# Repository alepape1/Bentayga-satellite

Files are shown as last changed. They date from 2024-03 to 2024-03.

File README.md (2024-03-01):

# Bentayga Cubesat

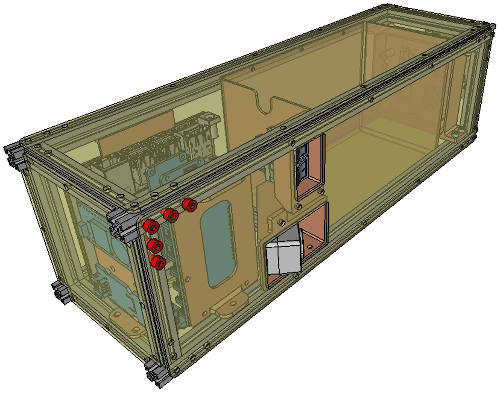
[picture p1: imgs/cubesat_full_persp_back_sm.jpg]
Bentayga Cubesat


## Description

This project describes the Bentayga 3U cubesat, developed by [IUMA](https://www.iuma.ulpgc.es/) at the [University of Las Palmas de Gran Canaria](https://www.ulpgc.es/).

The project is composed by three main parts:

- Structure made of 10x10 profiles, 3D printed parts and CNC milled FR4 fiberglass
- [Multispectral image acquisition](#multispectral-image-acquisition), composed by a Jetson Nano, 4 cameras with filters
- [Control and Flight manager](#flight-manager), composed by an Arduino MKR WAN 1310, with sensors such as GPS, temperature, humidity, barometer, RTC, IMU, and also controls the temperature of the batteries by activating heat pads.

---

## Bill Of Materials

[BOM](./bom_bentayga_cubesat.ods)

---

## [Assembly instructions](./assembly)

Assembly instructions are in [assembly directory](./assembly)

---

## [Structure](./cad)

Bentayga Cubesat

CAD files are in [Structure](./cad) directory.

## [Multispectral image acquisition](./CameraBoard)

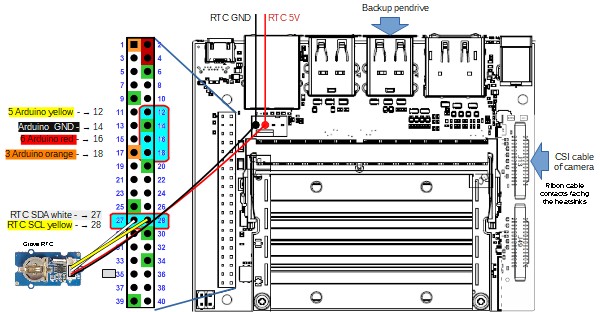
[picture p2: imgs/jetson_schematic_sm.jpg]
Jetson Nano connections


[Larger image of Jetson Nano connections](./imgs/jetson_schematic.jpg)

More information and source code is in [Camera board](./CameraBoard)

---

## [Flight manager](./Firmware)

The Flight Manager is responsible for gathering flight data from the IMU, sensors and transmitting it via LoRa to a ground station. It is also responsible of keeping batteries warm.

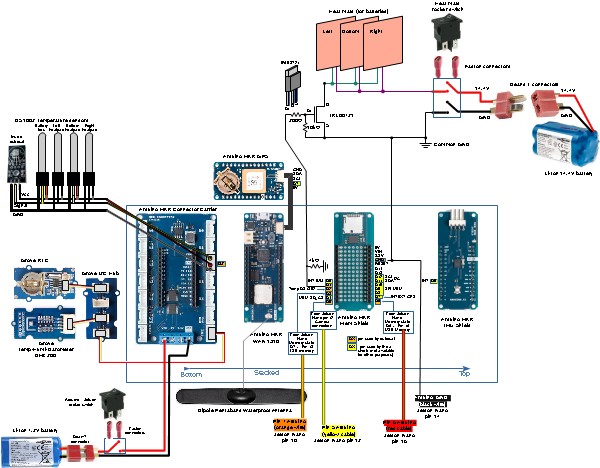
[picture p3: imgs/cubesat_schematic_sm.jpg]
Flight manager


[Larger image of electronics schematic](./imgs/cubesat_schematic.jpg)

More information and source code is in [Firmware](./Firmware)

---

## Contributing

If you wish to contribute to this code, please create a new branch from the develop branch and submit a pull request. 

---

## License

This code is licensed under the MIT License.

---

## CAD Images

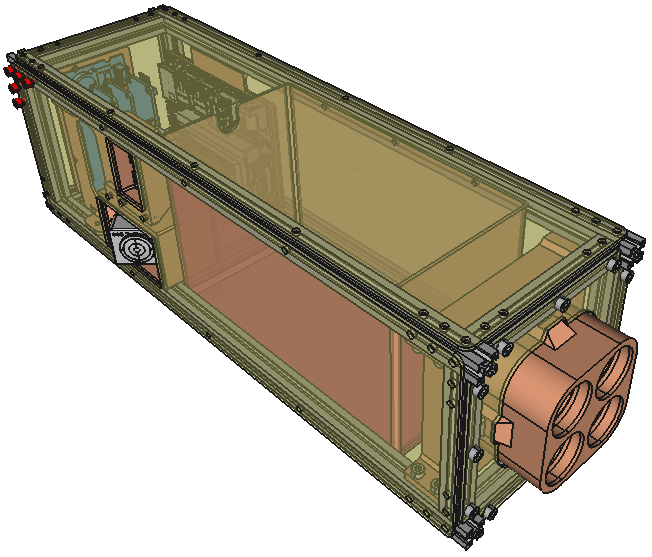
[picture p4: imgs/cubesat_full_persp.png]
Bentayga Cubesat front


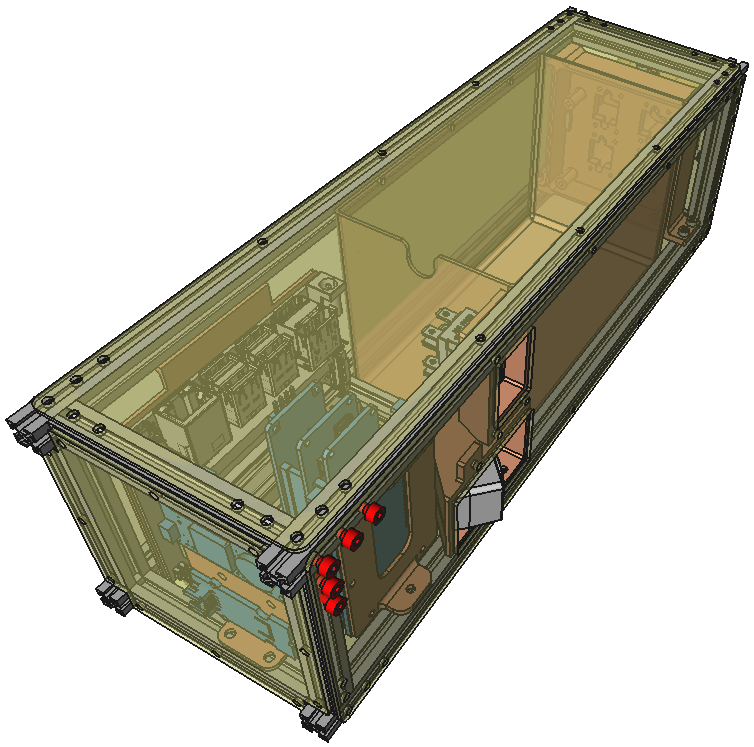
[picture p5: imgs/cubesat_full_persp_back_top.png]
Bentayga Cubesat back front


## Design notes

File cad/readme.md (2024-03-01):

# CAD files

There are 6 plates that have to be cutted or printed.

The references are as follows
Cielo and Tierra are the small sides, looking to the Sky and Earth.

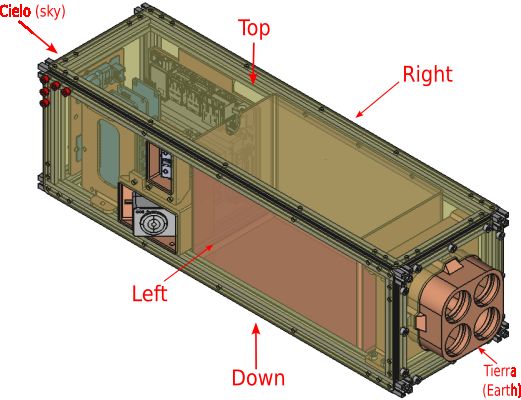
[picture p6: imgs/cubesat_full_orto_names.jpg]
References


Top and right plates are the placa_simple.
The others have the names in the file name.

## [DXF files](./dxf)

2D files for the plates, to cut them.

## [IGES files](./iges/placas)

3D files for the plates, to cut them.

## [FreeCAD files](./fcad)

Original FreeCAD files

## [PDF files](./pdf)

Files are for the plates, to laser cut.
Top and right plates use placa_simple.pdf

## [SVG files](./svg)

Also for the plates, you can edit them using Inkscape.

## [STEP files](./step)

These files are for the 3D parts, in a parametric format that most tools can read

## [STL files](./stl)

These files are for the 3D parts to print. You can print them without a support.

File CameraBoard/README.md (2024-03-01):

# Camera Capturing Platform

In this document the hardware and the software of the camera that is used to capture with the camera is described. 

## Hardware

### Jetson Nano Connections

The following scheme shows where to connect the external cables to the board that controls the camera capturing process. For the GPIO connections, refer to the [following list](#gpio-connection-list).

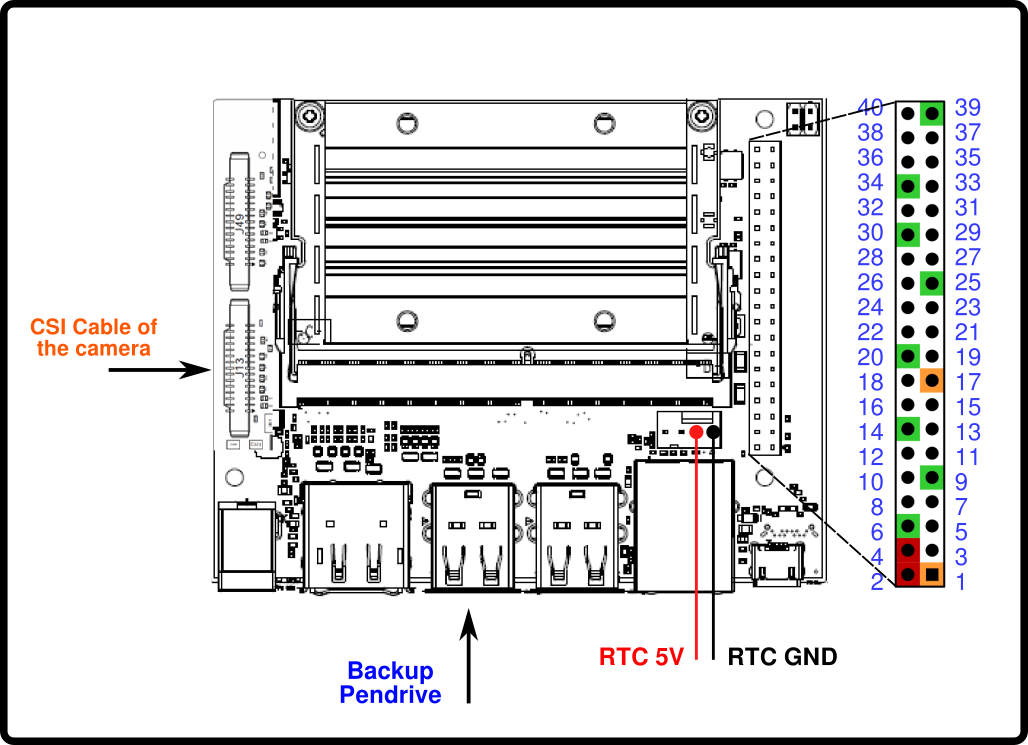
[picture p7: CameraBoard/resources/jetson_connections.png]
Jetson Nano Connection Scheme


#### GPIO connection list

* **Pins 1 - 6**: connect them to the six pin header of the camera.
* **Pin 12**: *Camera connection pin*. Connect it to the GPIO 5 in the Arduino.
* **Pin 16**: *Memory State LSB*. Connect it to the GPIO 6 in the Arduino.
* **Pin 18**: *Memory State MSB*. Connect it to the GPIO 7 in the Arduino.
* **Pin 27**: Connect it to the **SDA** pin of the **RTC**.
* **Pin 28**: Connect it to the **SCL** pin of the **RTC**.

## Software

### Installation

#### Initialize the process when the board is plugged in.

To execute the capturing code when the board is turn on, a custom service must be created. The service used is stored in the **.service** folder by the name of *camera-process.service* . The first step is to modify the document with the name of the current user and the current path of the *.sevice/execute_script.sh* file. Once the service points to the correct path, give execution permission to the *execute_script.sh* file. After that, execute the following commands to enable the service:

```bash
sudo cp .services/camera-process.service /etc/systemd/system
sudo systemctl start camera-process.service
sudo systemctl enable camera-process.service
```

The script will be executed once the board boots again. To stop the process after the start, run:

```bash
sudo systemctl stop camera-process.service
```

To check the status of the script, run the following command:

```bash
sudo systemctl status camera-process.service
```

To prevent the script to execute at the startup, run:

```bash
sudo systemctl disable camera-process.service
```

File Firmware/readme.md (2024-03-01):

# Flight manager:

Flight manager

[Larger image of electronics schematic](../imgs/cubesat_schematic.jpg)

The main stack of arduino boards is the following from bottom to top:

- MKR connector: https://docs.arduino.cc/hardware/mkr-connector-carrier
- MKR WAN 1310: https://docs.arduino.cc/hardware/mkr-wan-1310
- MKR MEM SHIELD: https://docs.arduino.cc/hardware/mkr-mem-shield
- MKR IMU SHIELD: https://docs.arduino.cc/hardware/mkr-imu-shield

Then there are other boards connected by I2C

- MKR GPS Shield: connect to the ESLOV connector https://docs.arduino.cc/hardware/mkr-gps-shield
- Grove - Temp&Humi&Barometer Sensor (BME280) https://www.seeedstudio.com/Grove-BME280-Environmental-Sensor-Temperature-Humidity-Barometer.html
- Grove - DS1307 RTC (Real Time Clock) for Arduino https://www.seeedstudio.com/Grove-RTC-DS1307.html

The temperature sensors are connected directly by Onewire protocol:

- DS18B2 temperature sensors [see below](#Temperature-sensors)

Finally, the heatpads are connected through a board that includes the MOSFET to control them (we have soldered the board) [see below](#Temperature-control)

### Requirements

This code requires the following libraries:
- Wire.h
- MS5x.h
- MKRIMU.h
- LoRa.h

Using the Arduino Library manager, search and install the following packages:

* BNO055 - Adafruit; and it dependencies.
* BM280 - Adafruit; and it dependencies.
* Groove RTC DS1307 - Speeed Studio
* OneWire https://playground.arduino.cc/Learning/OneWire
* Dallas Temperature: https://www.milesburton.com/w/index.php/Dallas_Temperature_Control_Library

### Setup

The Flight Manager should be connected to an IMU and a barometric pressure sensor. The LoRa module should also be properly connected.

### Usage

Upon startup, the Flight Manager will attempt to connect to the barometric pressure sensor. Once connected, it will continuously poll the sensor for data and transmit it via LoRa. Flight data is formatted into a byte array that includes start and stop bytes, as well as the following data:
- Roll
- Pitch
- Heading
- Temperature
- Pressure
- Sea level pressure
- Altitude
- Corrected altitude

In addition to transmitting the data, the Flight Manager also prints it to the serial monitor.

-------------------

## [Temperature sensors](./temperature)

Arduino code to identify and request temperature from the OneWire
 [DS18B20](https://www.analog.com/media/en/technical-documentation/data-sheets/ds18b20.pdf) temperature sensor, and to control the heatmats

Use libraries:

- https://playground.arduino.cc/Learning/OneWire
- https://www.milesburton.com/w/index.php/Dallas_Temperature_Control_Library

The cubesat has five DS18B20 temperature sensors, whose internal codes referred to the cubesat laid down and from the camera side, are:

Sensors inside the battery box
- Right (Derecha):  28 53 6E 95 F0 01 3C EE (waterproof sensor)
- Left (Izquierda): 28 37 50 95 F0 01 3C D7 (waterproof sensor)
- Down (Bajo):      28 7A EF 95 F0 01 3C C8 (waterproof sensor)
- Inside box:       28 55 B3 95 F0 01 3C EE (waterproof sensor)
- Inside cubesat:   28,FF 10 4B 20 18 01 10 (PCB sensor with resistor)

---

## Reference

Since there are 5 temperature sensors, 3 of them at the sides of the batteries. To know which sensor is each of them, the reference is taken from the following picture, considering I the left (Izquierda), and R the right (Derecha)

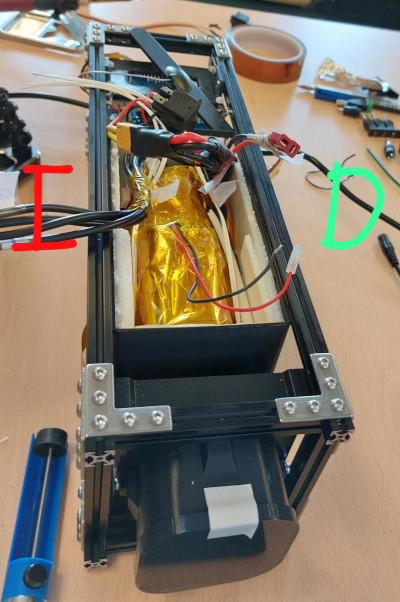
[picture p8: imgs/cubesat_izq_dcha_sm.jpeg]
Bentayga Cubesat Reference


### [Detect sensor ID](./temperature/detect_ds1820_tempsens_id/)

Get the sensor ID, better to have just one sensor to know the ID, because it will print all the sensors ID found.

As explained in the datasheet, there are two options for the sensor connection, we have used the one with external supply, using as VDD the 5V of the Arduino. 
A 4.7 Ohm resistor is needed, but the board sensor already has one. In the other cases, you will need to connect it.

Various sensor can be connected in multidrop, with multiple slaves.

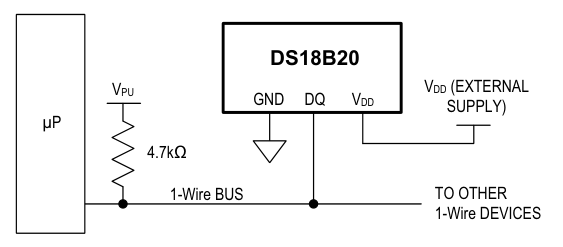
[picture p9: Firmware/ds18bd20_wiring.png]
DS18D20 wiring


### [Get sensor temperature](./temperature/get_temp_ds18b20_wid/)

Having the IDs of the sensor, it will request their temperatures.

Since one of the sensors is in a board with a resistor, an additional resistor is not needed.

### [Temperature control](./temperature/tempsens_heatpad)

It has been tested with two sensors and two heatmats. The two heatmats are connected in parallel.
Since one of the sensors is in a board with a resistor, an additional resistor is not needed.

Using the MOSFET [IRLB8721](https://www.infineon.com/cms/en/product/power/mosfet/n-channel/irlb8721/) to control the heatmats.

The connections of the MOSFET are the following:
 - Gate (G) goes directly to a PWM output pin of the Arduino.
 - Source (S) goes to the GND
 - Drain (D) goes to one of the wires of the heatpad, the other wire of the heatpad goes to the external battery. We have connected two heatpads in parallel, since the MOSFET has an absolute maximum continous drain current of 62A at VGS=10V and T=25C

**This code is for a battery of 12V or less**. We are using a 7.2V or 7.4V battery. In case you use a 14V battery you have to use PWM (analogueWrite) for the Full-ON cases, and have a maximum value of 212 (and test it). I think it might be a good idea to use the 14V battery with the PWM.

The battery GND is connected with the Arduino GND.

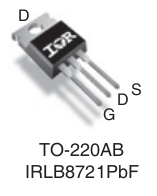
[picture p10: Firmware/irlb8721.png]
IRLB8721


Heatpads: https://es.rs-online.com/web/p/alfombrillas-calefactoras/0245512

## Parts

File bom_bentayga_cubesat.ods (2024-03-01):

 |  | SKU |  |  | Info | Vendor
1 | Jetson Nano Development Kit | 945-13450-0000-100 | 152.02 € | 152.02 € | https://developer.nvidia.com/embedded/jetson-nano-developer-kit | https://es.rs-online.com/web/p/kits-de-desarrollo-de-procesadores/1999831
1 | Arduino MKR Connector Carrier | ASX00007 | 20.30 € | 20.30 € | https://docs.arduino.cc/hardware/mkr-connector-carrier | https://store.arduino.cc/products/arduino-mkr-connector-carrier-grove-compatible
1 | Arduino MKR WAN 1310 | ABX00029 | 39.60 € | 39.60 € | https://docs.arduino.cc/hardware/mkr-wan-1310 | https://store.arduino.cc/products/arduino-mkr-wan-1310
1 | Arduino MKR Mem Shield | ASX00008 | 20.30 € | 20.30 € | https://docs.arduino.cc/hardware/mkr-mem-shield | https://store.arduino.cc/products/arduino-mkr-mem-shield
1 | Arduino MKR IMU Shield | ASX00002 | 25.20 € | 25.20 € | https://docs.arduino.cc/hardware/mkr-imu-shield | https://store.arduino.cc/products/arduino-mkr-imu-shield
1 | Arduino MKR GPS Shield | ASX00017 | 34.80 € | 34.80 € | https://docs.arduino.cc/hardware/mkr-gps-shield | https://store.arduino.cc/products/arduino-mkr-gps-shield
1 | Sandisk Ultra MicroSDHC 32GB UHS-I U1 A1 Clase 10 | SDSQUA4-032G-GN6MA | 7.49 € | 7.49 € | For the MKR Mem Shield | https://www.pccomponentes.com/sandisk-ultra-microsdhc-32gb-uhs-i-u1-a1-clase-10
1 | Pendrive 64 GB Verbatim | 98711 | 13.28 € | 13.28 € | For the Jetson Nano | https://es.rs-online.com/web/p/pendrives/2444627
1 | Sandisk Ultra Fit 128GB USB 3.1 | SDCZ430-128G-G46 | 19.99 € |  | For the Jetson Nano | https://www.pccomponentes.com/sandisk-ultra-fit-128gb-usb-31
1 | Grove - Hub I2C Seeed Studio | 103020006 | 3.22 € | 3.22 € | https://www.seeedstudio.com/Grove-I2C-Hub.html | https://es.rs-online.com/web/p/kits-de-desarrollo-inalambricos-y-de-comunicacion/1743256
1 | Seeed Studio Grove - Temp and Humi and Barometer Sensor | 101020193 | 19.51 € | 19.51 € | https://www.seeedstudio.com/Grove-BME280-Environmental-Sensor-Temperature-Humidity-Barometer.html | https://es.rs-online.com/web/p/kits-de-desarrollo-de-sensores/1845082
2 | Grove - DS1307 RTC | 101020013 | 7.04 € | 14.08 € | https://www.seeedstudio.com/Grove-RTC-DS1307.html | https://es.rs-online.com/web/p/kits-de-desarrollo-de-relojes-y-temporizadores/1845075
1 | Dipole Pentaband Waterproof Antenna | X000016 | 4.80 € | 4.80 € | Antenna for GSM 850 / 900 / 1800 / 1900 MHz and UMTS bands | https://store.arduino.cc/products/dipole-pentaband-waterproof-antenna
1 | MOSFET IRLB8721 | IRLB8721PBF | 1.14 € | 1.14 € | N-Channel MOSFET with low Vgs so it can be driven with the 3.3V logic values of Arduino MKR | https://es.rs-online.com/web/p/mosfet/7259322
1 | Grove - Universal 4 Pin Buckled 5cm Cable (5 PCs Pack) | 110990036 | 1.89 € | 1.89 € | https://www.seeedstudio.com/Grove-Universal-4-Pin-Buckled-5cm-Cable-5-PCs-Pack.html | https://www.digikey.es/es/products/detail/seeed-technology-co-ltd/110990036/5482563
3 | Heater Mat 50x75 mm, 12 V DC, 3.75 W | 245-512 | 29.56 € | 88.68 € | Silicone Heater Mats for the batteries | https://es.rs-online.com/web/p/alfombrillas-calefactoras/0245512
2 | Panasonic BR1225 Button Battery, 3V, 12.5mm Diameter | BR-1225/BN | 1.94 € | 3.88 € | For the RTCs, BR are more suitable for low temperatures than CR | https://es.rs-online.com/web/p/pilas-de-boton/7450929
1 | Ansmann 7.2V Lithium-Ion Rechargeable Battery Pack, 2.6Ah | 2447-3002 | 35.02 € | 35.02 € | Battery for Arduino 7.2V 2600mAh | https://es.rs-online.com/web/p/baterias-recargables/7760857
1 | Ansmann 14.4V Lithium-Ion Rechargeable Battery Pack, 2.6Ah | 2447-3036-520 | 72.63 € | 72.63 € | Battery for Heatmats 14.4V 2600mAh | https://es.rs-online.com/web/p/baterias-recargables/8114693
2 | LIPO Battery 7.4V 6000mAh 2S 5C |  | 52.50 € | 105.00 € | Batteries for Jetson Nano | https://www.hobbytelde.es/productos/electronica-r-c-/232-bateria-lipo-7-4v-6000-mah--2s-50c-especial-crawler.html
2 | Deans T male connector | T-DEANM | 0.93 € | 1.86 € | Connectors for Li-ion batteries | http://lopacan.es/articulo.php?idart=34048
2 | Deans T female connector | T-DEANH | 0.93 € | 1.86 € | Connectors for Li-ion batteries (solder female on battery side) | http://lopacan.es/articulo.php?idart=34049
2 | Rocker switch 4 pin 2 positions. KCD1 - 104 AC 250V 6A | KCD1-104 | 1.85 € | 3.70 € | Switch for batteries. One for Arduino and Jetson Nano, the other for heat mats | http://lopacan.es/articulo.php?idart=20779
8 | Faston female terminal 6.4mm isolated | TE506AIS | 0.18 € | 1.44 € | To connect the switches | http://lopacan.es/articulo.php?idart=30288
1 | Kapton Tape |  | 2.47 € | 2.47 € | Kapton tape (high temperature resistant) to wrap the batteries in aluminum foil, with the heatmats and temperature sensors inside | https://www.hta3d.com/en/kapton-tape-polyimide-bga-30mm
 | Makerbeam profiles for the structure
4 | Makerbeam 10x10 340.5mm |  |  | 17.25 € | Get a 1500 mm profile and cut | https://www.makerbeam.com/makerbeam-1500mm-1p-black-makerbeam.html
10 | Makerbeam 10x10 80mm |  |  | 17.25 € | Get a 1500 mm profile and cut | https://www.makerbeam.com/makerbeam-1500mm-1p-black-makerbeam.html
14 | Openbeam cuts |  | 2.25 € | 31.50 € | Cut the above profiles, OpenBeam is chosen because no need to tap | https://www.makerbeam.com/cut-openbeam.html
1 | Makerbeam right angle brackets (12) |  | 7.25 € | 7.25 € | You need less, but it is always useful to have spare, and for the building process | https://www.makerbeam.com/makerbeam-right-angle-brackets-12p.html
1 | Makerbeam T brackets (12) |  | 7.25 € | 7.25 € | You need less, but it is always useful to have spare, and for the building process | https://www.makerbeam.com/makerbeam-t-brackets-12p.html
1 | Makerbeam 6mm M3 square headed bolts (250) |  | 13.98 € | 13.98 € |  | https://www.makerbeam.com/makerbeam-square-headed-bolts-6mm-250p-for-makerbe.html
1 | Makerbeam 10mm M3 square headed bolts (100) |  | 8.25 € | 8.25 € |  | https://www.makerbeam.com/square-headed-bolts-10mm-100p-for-makerbeam.html
1 | Self locking M3 nuts (100) |  | 4.65 € | 4.65 € |  | https://www.makerbeam.com/makerbeam-self-locking-nuts-100p.html
1 | M3 nuts (250) |  | 6.55 € | 6.55 €
2 | T-slot nuts (25) |  | 15.98 € | 31.96 € |  | https://www.makerbeam.com/makerbeam-t-slot-nuts-for-makerbeam-25p.html
2 | FR4 fiber glass plate 500x300x1.5mm |  | 8.15 € | 16.30 € | To be cut with a laser cutter or CNC mill | https://www.ahltec.de/shop/de/500-mm-x-300-mm-48-68-83-186.html
 |  |  |  | 836.36 €

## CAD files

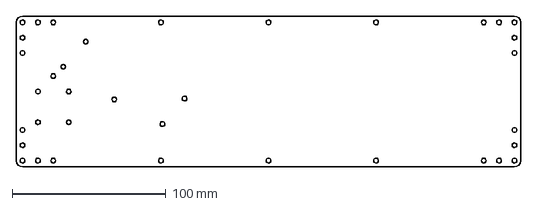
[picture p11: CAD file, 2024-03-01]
cad/dxf/placa_down_dipole.dxf
328.0 x 98.0 mm

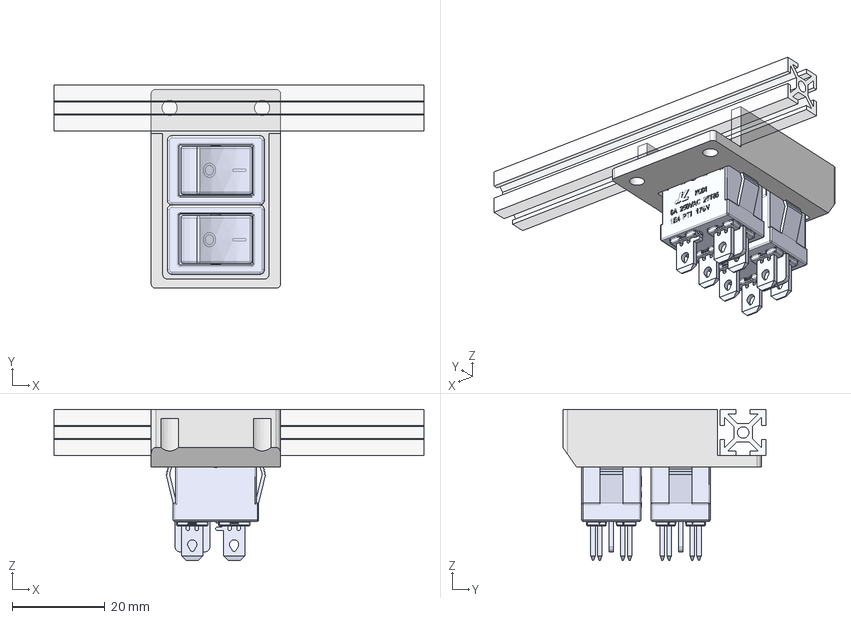
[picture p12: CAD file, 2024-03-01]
cad/fcad/switch_support_cut.FCStd
80.0 x 44.0 x 32.7 mm
Switch KCD1-104_micro
Switch KCD1-104_heatmats
aluprof_10
switch_cut2_refined

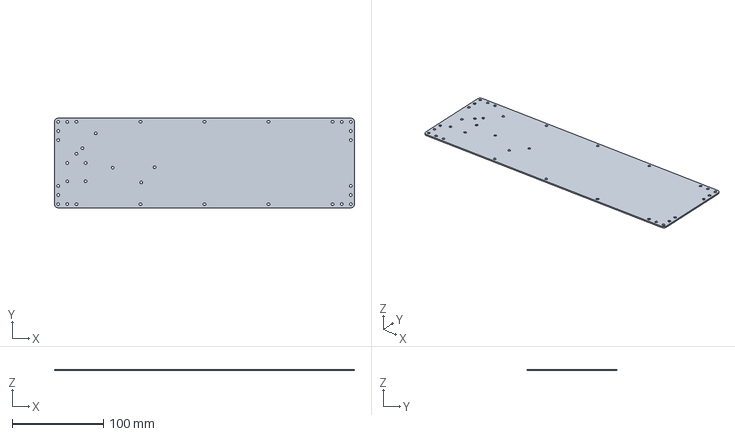
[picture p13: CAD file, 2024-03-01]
cad/iges/placas/placa_down_dipole.iges
328.0 x 98.0 x 1.50 mm

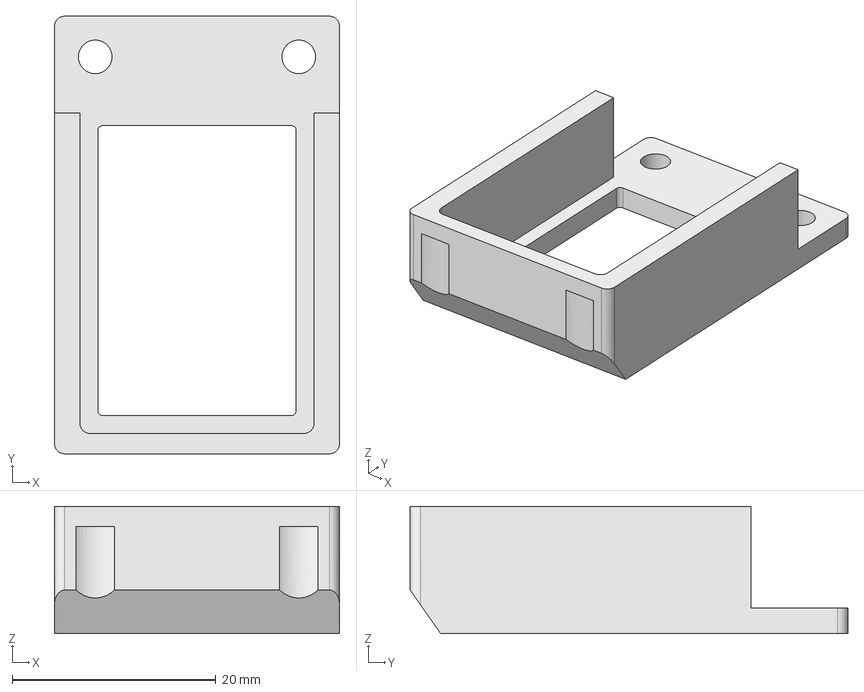
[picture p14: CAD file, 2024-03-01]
cad/step/switch_support_cut.step
28.0 x 43.0 x 12.5 mm

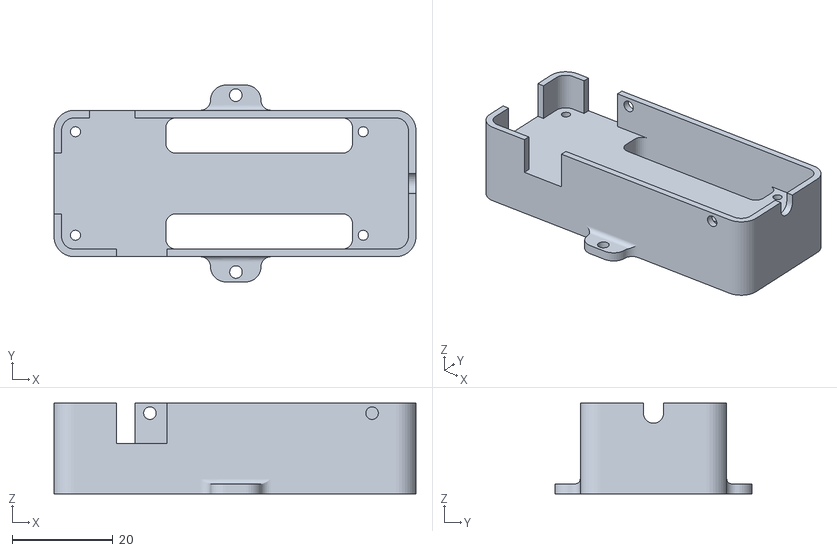
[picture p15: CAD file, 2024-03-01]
Software/working_on/mkr1310v3-bottom.stl
71.7 x 39.0 x 18.0

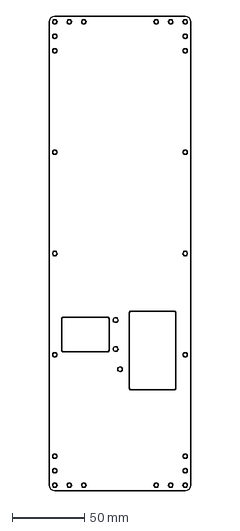
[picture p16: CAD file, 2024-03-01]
cad/dxf/placa_left_switch_camera.dxf
98.0 x 328.0 mm

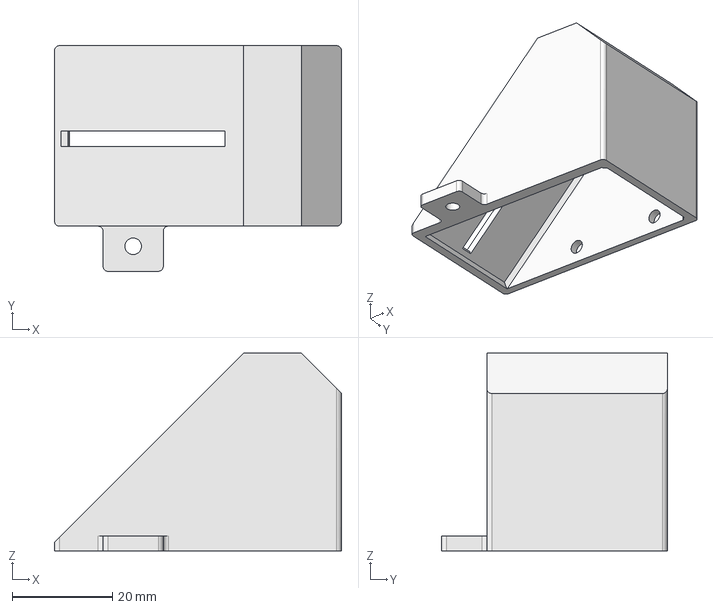
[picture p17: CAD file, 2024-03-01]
cad/fcad/camera_support_toprint.FCStd
57.2 x 45.0 x 39.4 mm

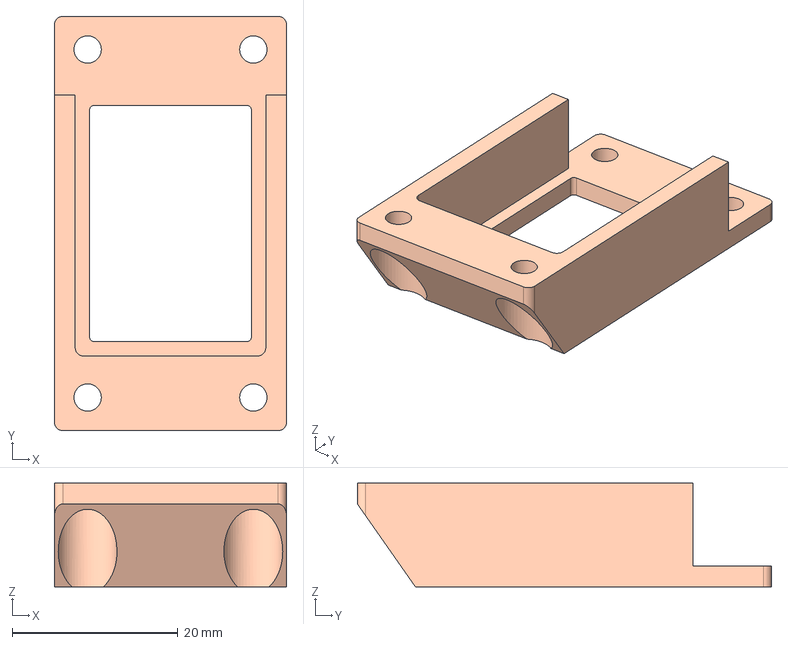
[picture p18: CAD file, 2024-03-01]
cad/step/switch_support.step
28.0 x 50.0 x 12.5 mm

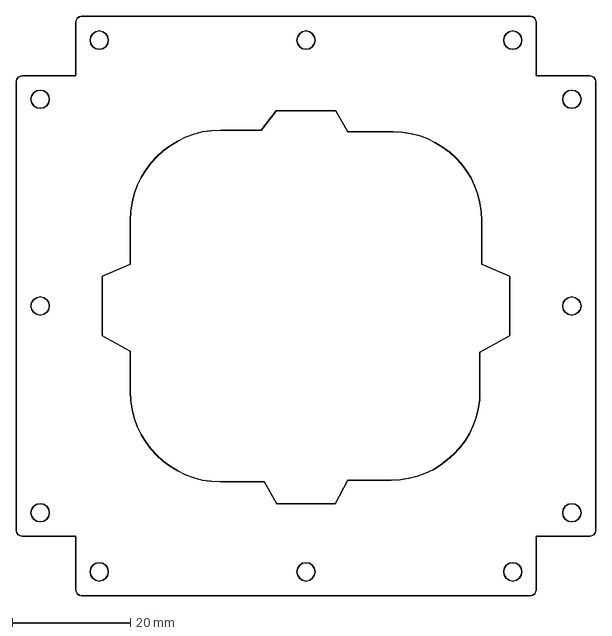
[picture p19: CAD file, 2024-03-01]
cad/dxf/placa_tierra.dxf
98.0 x 98.0 mm

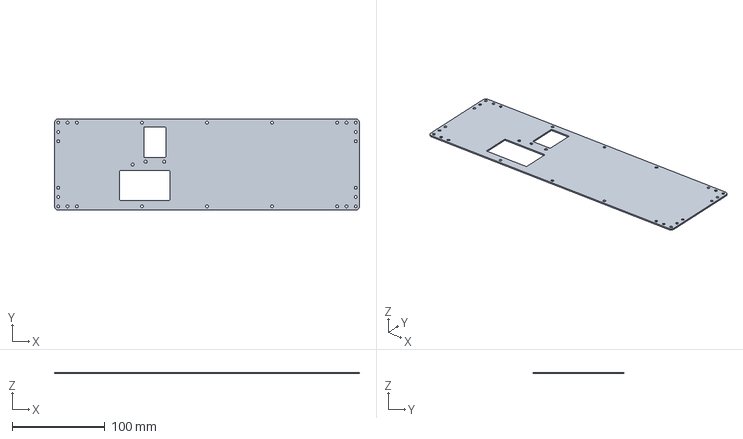
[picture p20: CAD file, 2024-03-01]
cad/iges/placas/placa_left_switch_camera.iges
328.0 x 98.0 x 1.50 mm

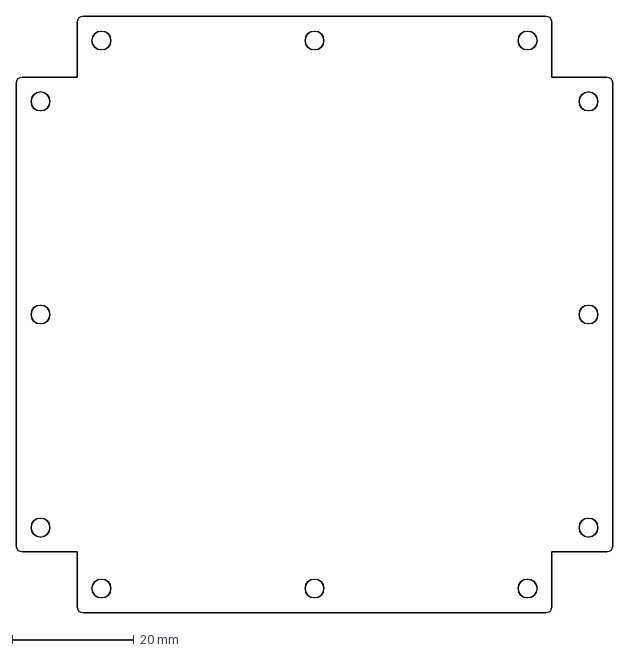
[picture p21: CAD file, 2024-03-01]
cad/dxf/placa_cielo.dxf
98.0 x 98.0 mm

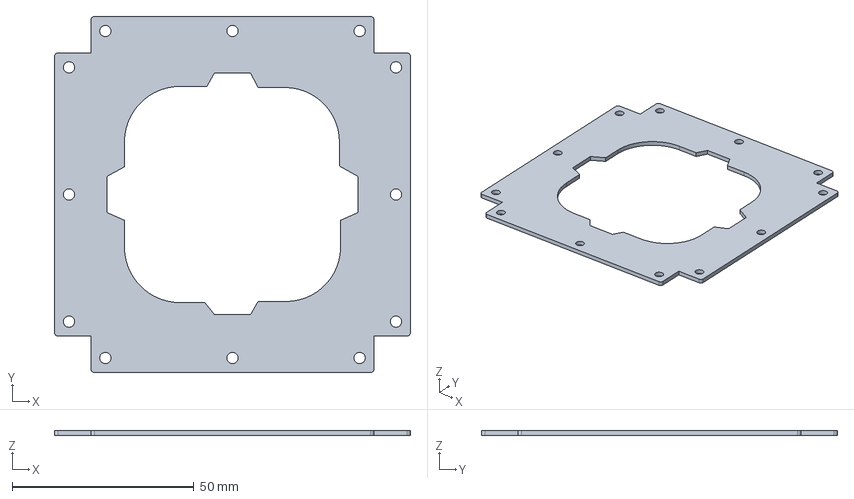
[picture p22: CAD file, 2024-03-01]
cad/iges/placas/placa_tierra.iges
98.0 x 98.0 x 1.50 mm

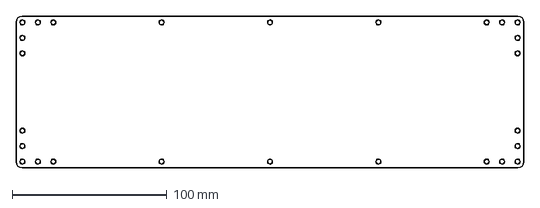
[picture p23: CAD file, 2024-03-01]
cad/dxf/placa_simple.dxf
328.0 x 98.0 mm

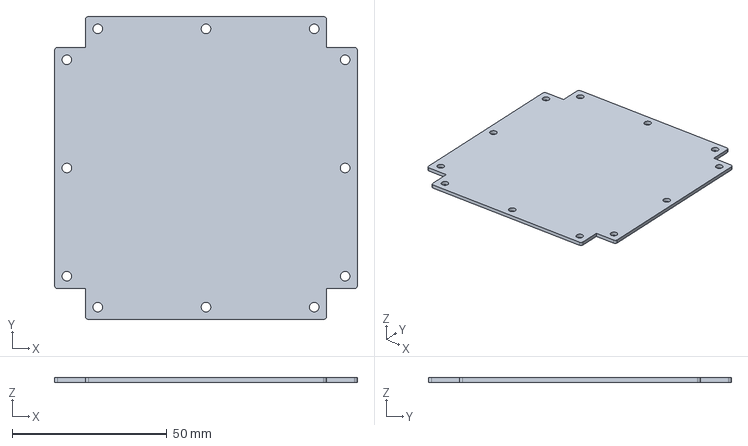
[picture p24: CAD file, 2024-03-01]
cad/iges/placas/placa_cielo.iges
98.0 x 98.0 x 1.50 mm

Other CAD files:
cad/iges/placas/placa_simple.iges
cad/step/camera_support_toprint.step
cad/stl/camera_support_toprint.stl
cad/stl/switch_support.stl
cad/stl/switch_support_cut.stl

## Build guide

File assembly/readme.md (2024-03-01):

# Assembly instructions

Before assembling the cubesat, have all the electronics connected and make sure that they work. Disconnect the batteries and electronics before the assembly. 

Check the CAD files, and get all the 3D pieces printed and the plates milled.

Get all the components of the [BOM](./../bom_bentayga_cubesat.ods)
Have pliers, Allen keys, screwdrivers, small zip ties, .... Silicone would be very useful to place the t-slot nuts and prevent them from sliding.

The cubesat has 6 faces, they will be named according to this reference:

References

---

## Warning

Take into account that once you close the profiles, you cannot place square bolts and in many times even nuts.

The following picture shows that you cannot add any nut or bolt in the blue profile. In the inner slot of the green profile you can add nuts, but not bolts.

Therefore, before closing a profile think if all the nuts and bolts are placed, and what are you going to attach to the profile.

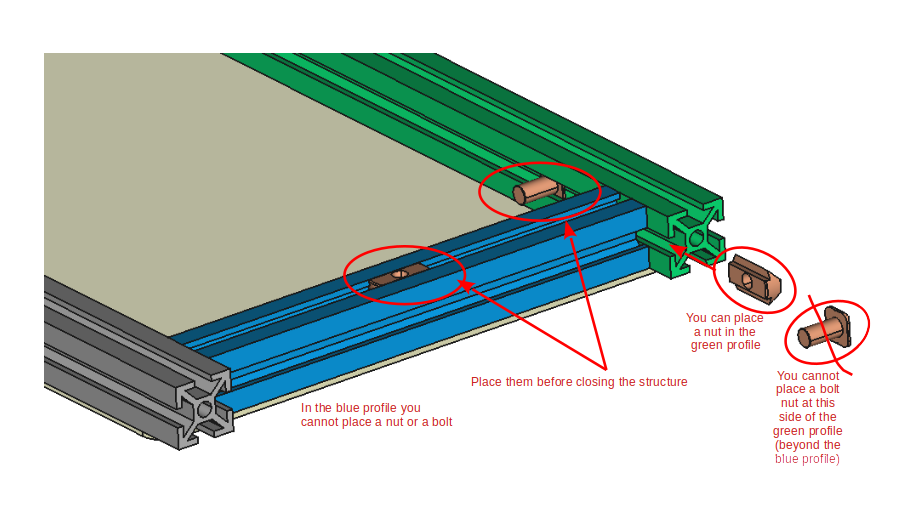
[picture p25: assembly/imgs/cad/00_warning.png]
nut_warning


It is recommended to read all the instructions once before starting the assembly because there are some information that it is useful to know beforehand.

---

## Place nuts in 80mm-profiles

There are eight 80mm-profiles at the two squared faces of the cubesat (four at each face). The figure shows one of this faces.

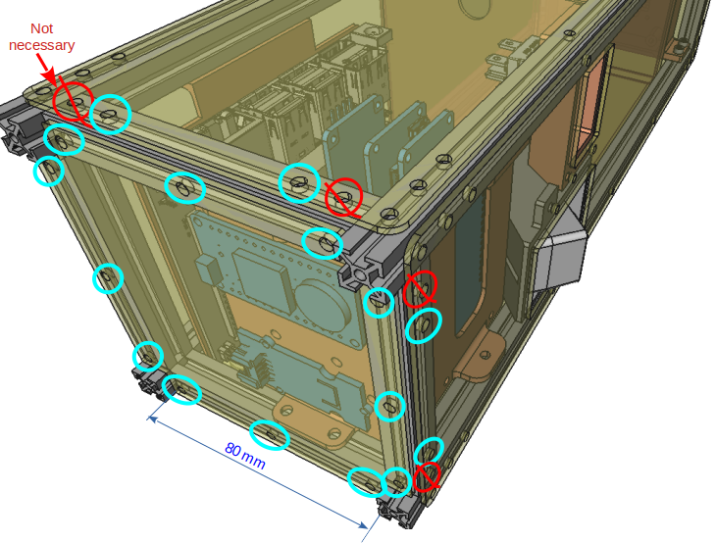
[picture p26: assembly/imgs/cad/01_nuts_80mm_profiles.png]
nuts 8mm


All these profiles have 3 sliding nuts in one side and 2 in the other (you could put 4 but it is not necessary). These nut holes are marked in turquoise circles in the figure. The red circles indicate that these nuts are optional.

Place 2 and 3 sliding nuts in two consecutive sides of these eight profiles.

We recommend that you align these nuts with the holes of the plates and put some silicone to prevent the nuts from sliding. So they are easier to screw with the bolts.
It is not necessary to be super exact, since the silicone leaves room for moving the nuts a little bit. You don't need to wait until the silicone is dry.

The following pictures shows the process.

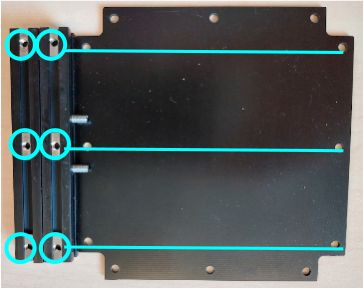
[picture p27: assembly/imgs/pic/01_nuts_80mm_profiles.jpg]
nuts 8mm


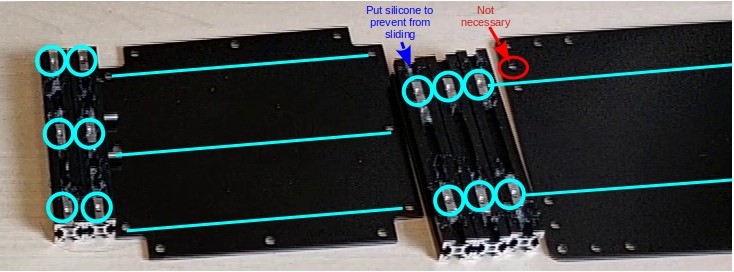
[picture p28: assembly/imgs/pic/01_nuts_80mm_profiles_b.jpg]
nuts 8mm


---

## Assemble the Down panel

Now that you have nuts in the 80mm-profiles, we are going to assemble the Down plate.

The profile at the Cielo side has also a 3D part attached to it (see next figure).

Include two [M3 6-mm square headed bolts](https://www.makerbeam.com/makerbeam-square-headed-bolts-6mm-250p-for-makerbe.html).

Don't put silicone on these bolts

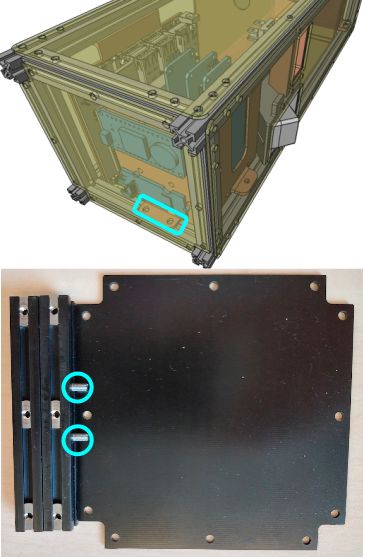
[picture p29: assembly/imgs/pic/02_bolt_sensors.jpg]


Put in the long 340.5mm profiles five sliding nuts, aligned to the plate holes. It is not necessary to put silicone in these nuts, but you could.

Now put the Down plate over the four profiles attached to it, and screw the M3 4mm Hexagon socket button head screws (ISO7380). Take care that the 80mm profiles have the nuts facing the correct side.

Place the long profiles to be symmetrical, leaving the same distance in each side.

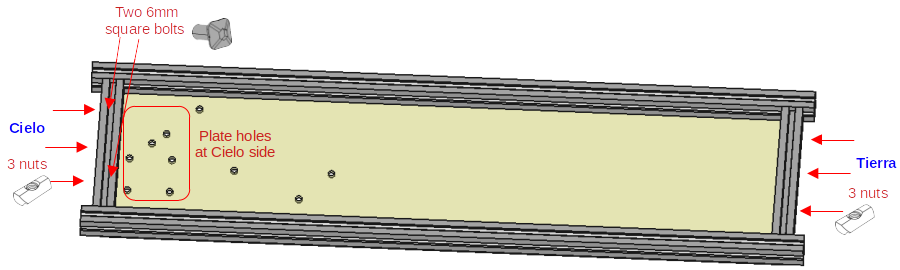
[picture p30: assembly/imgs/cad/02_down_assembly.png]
Down CAD


The result should look like this

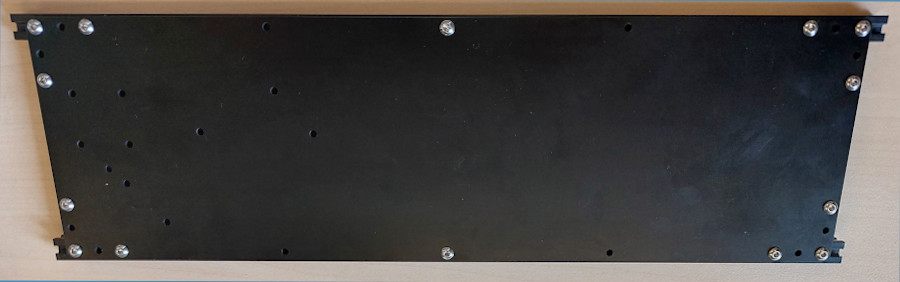
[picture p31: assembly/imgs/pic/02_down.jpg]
Down picture


---

## Attach the I2C hub to the Down plate

Use three M2 bolts around 6mm long. We have used one steel bolt and nut, and the other two plastic, but you can choose the material.

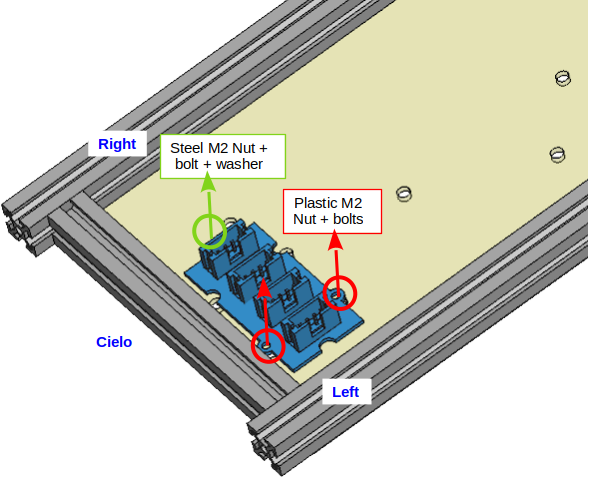
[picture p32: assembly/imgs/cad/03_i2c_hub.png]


Picture from the bottom:

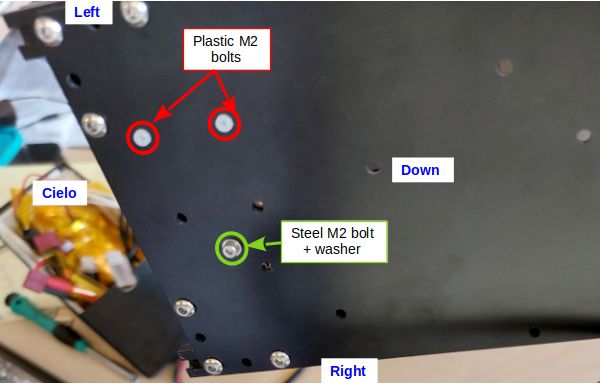
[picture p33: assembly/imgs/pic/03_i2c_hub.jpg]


---

## Attach the Jetson Nano

First attach the Jetson Nano to its 3D printed support.

Then take two M3 square headed 6mm bolts and attach the lower part of the Jetson Nano support to it. Then put two M3 self locking nuts, tighten but not so much so you can still slide the Jetson Nano along the profile.

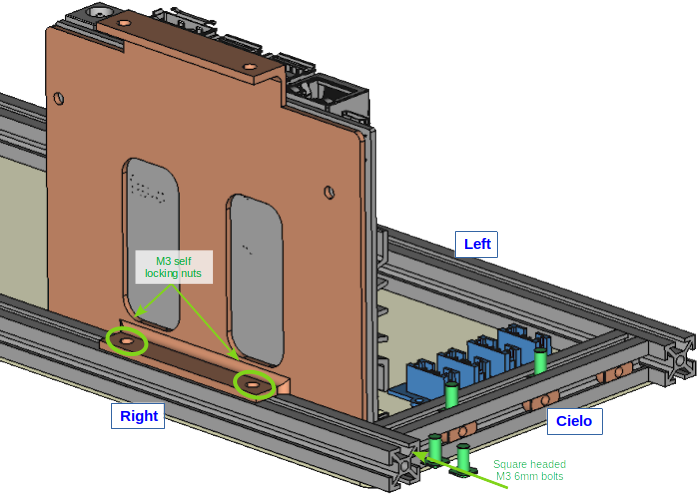
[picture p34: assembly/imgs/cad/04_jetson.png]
Jetson CAD


Picture from Top:

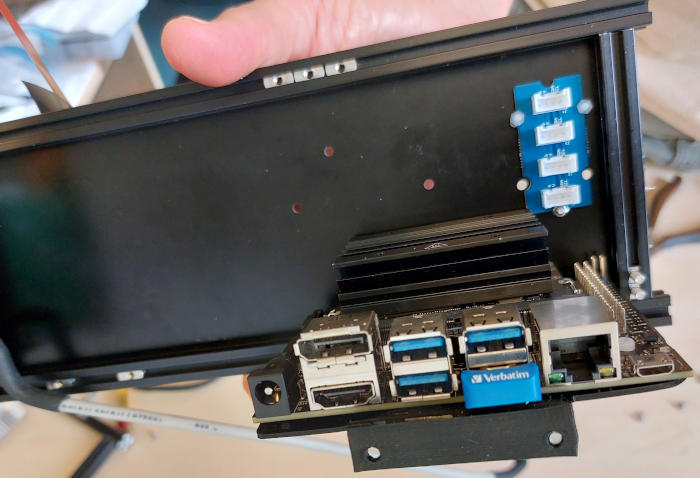
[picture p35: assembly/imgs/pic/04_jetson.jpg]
Jetson picture


---

## Attach the sensors support

First attach the four boards to the support with M2 plastic bolts and nuts.

-  MKR GPS Shield: connect to the ESLOV connector https://docs.arduino.cc/hardware/mkr-gps-shield
-  Grove - Temp&Humi&Barometer Sensor (BME280) https://www.seeedstudio.com/Grove-BME280-Environmental-Sensor-Temperature-Humidity-Barometer.html
- Two Grove - DS1307 RTC (Real Time Clock) for Arduino https://www.seeedstudio.com/Grove-RTC-DS1307.html

Attach the bottom of the support to the profile. There should be two 6mm square headed bolts in this profile, as indicated in the assembling of the Down panel.

Put the self locking nuts as in the Jetson Nano support, but not too tight to be able to slide the support later.

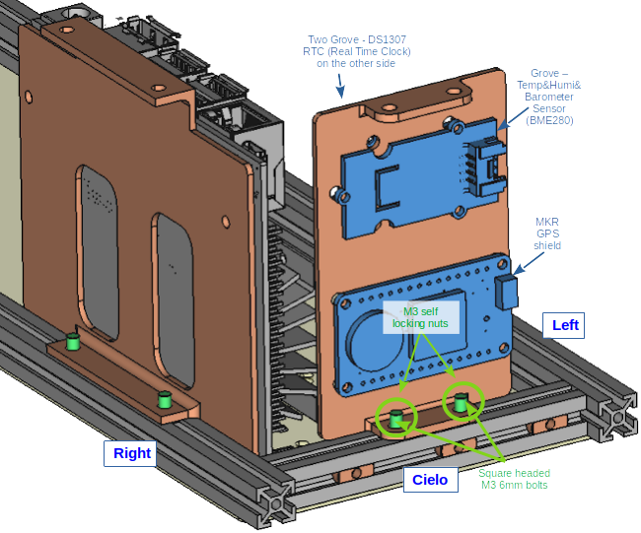
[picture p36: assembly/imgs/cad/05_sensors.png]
Sensors CAD


Picture from back:

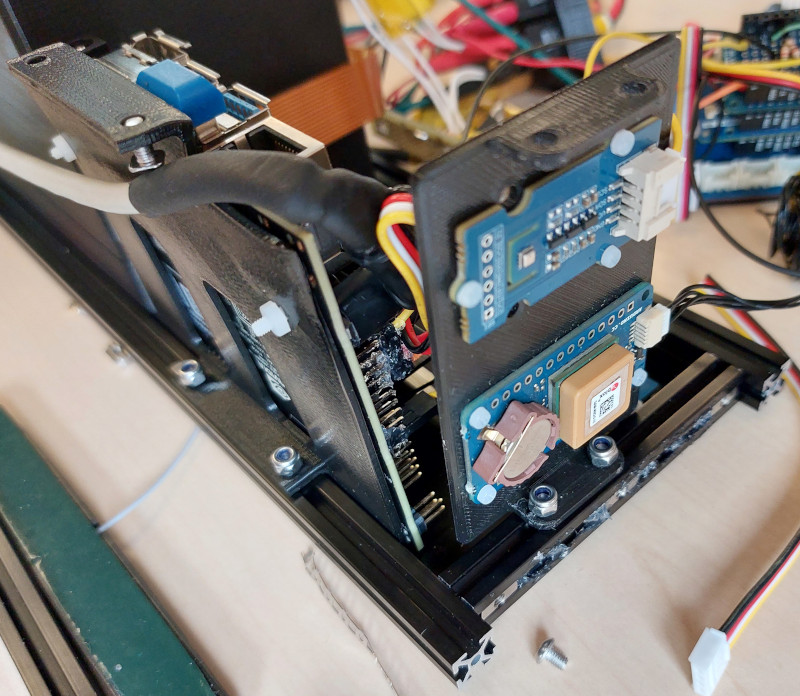
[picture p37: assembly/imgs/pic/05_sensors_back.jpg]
Sensors back picture


Picture from Top:

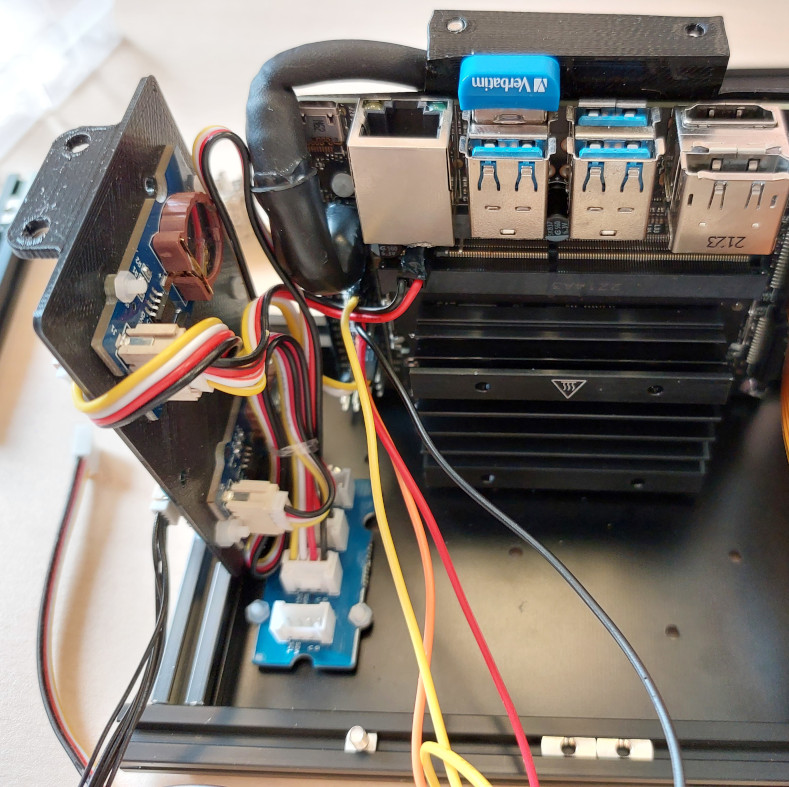
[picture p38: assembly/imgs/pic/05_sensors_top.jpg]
Sensors top picture


---

## Attach the Arduino stack

Before attaching the support, **insert four sliding nuts in the profile**. They will be needed for the small camera support, and to contain the battery box.

Also insert two sliding nuts in the opposite profile (Right side) to contain the battery box.

First the Arduino stack should be mounted, also make sure that the components in the MKR MEM Shield have been soldered, and from this shield go the wires to the Jetson Nano and MOSFET for the heat pads (which is soldered in a different board).

The stack of Arduino boards is the following from bottom to top:

- MKR connector: https://docs.arduino.cc/hardware/mkr-connector-carrier
- MKR WAN 1310: https://docs.arduino.cc/hardware/mkr-wan-1310
- MKR MEM SHIELD: https://docs.arduino.cc/hardware/mkr-mem-shield
- MKR IMU SHIELD: https://docs.arduino.cc/hardware/mkr-imu-shield

Attach this stack to the 3D printed support and in the same way as the previous support, attach it to the profile with a 6mm M3 square headed bolt and a self locking nut. Do tighten the nut too much to allow sliding.

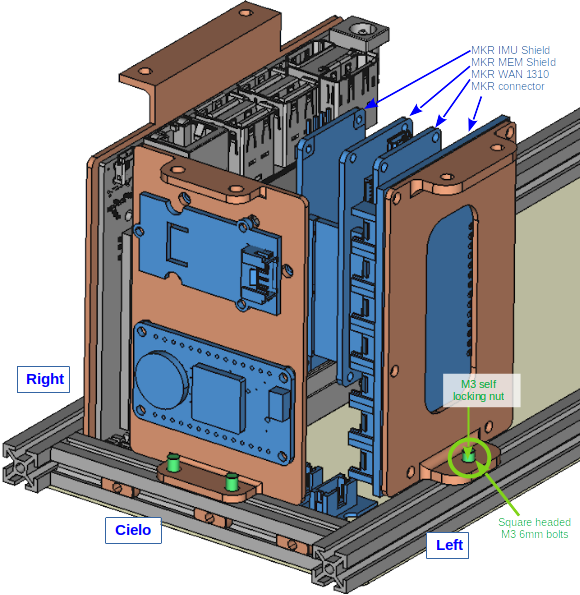
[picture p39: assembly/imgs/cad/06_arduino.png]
Arduino CAD


Picture from Top (the IMU shield was missing in the picture)

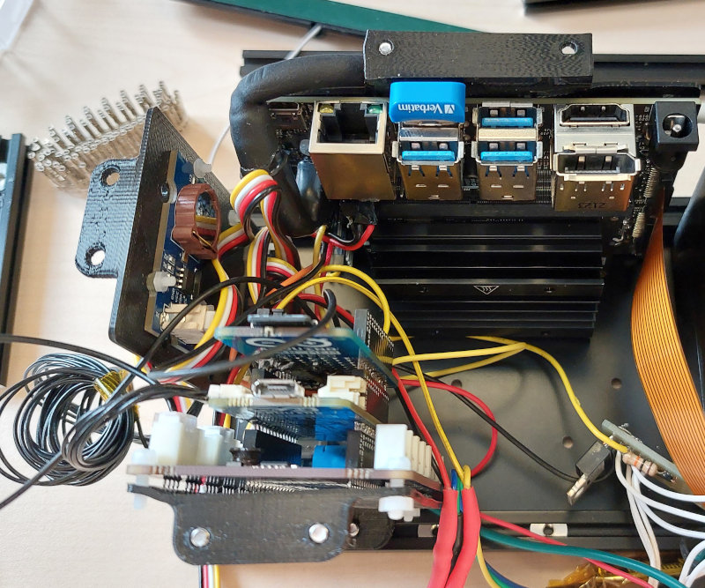
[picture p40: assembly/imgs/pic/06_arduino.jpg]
Arduino top picture


---

## Attach the multispectral camera

Using four 12-mm square headed bolts and self locking nuts, attach the multispectral camera at the Tierra side as shown in the figure:

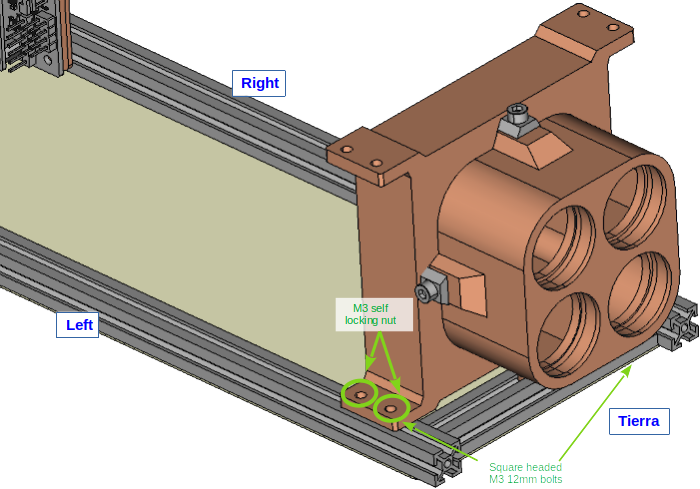
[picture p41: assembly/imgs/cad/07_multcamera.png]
Multispectral camera CAD


---

## Insert the battery box

Just put it in place to check the dimensions

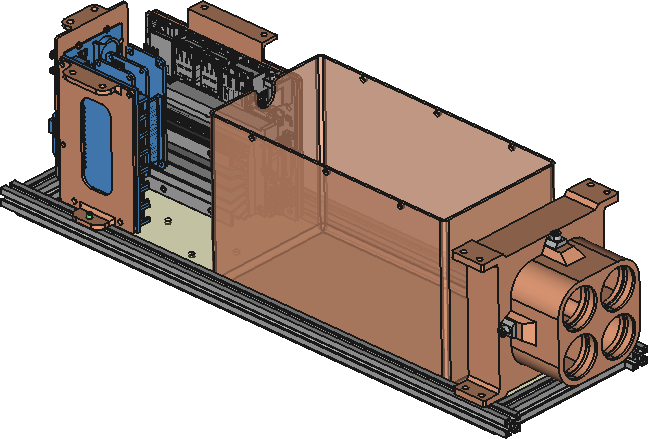
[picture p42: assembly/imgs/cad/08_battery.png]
Battery box CAD


---

## Attach the small camera support

Fist attach the original camera support to the 3D printed support, using two M3 6mm counter sunk bolts with self locking nuts.

Then use sliding nuts and tow hex button 4mm bolts to attach it to the profile. Do not tighten it to strong, so it can slide along the profile.

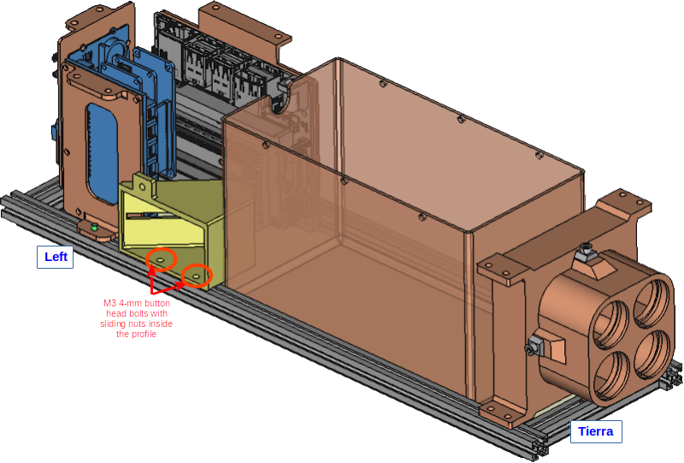
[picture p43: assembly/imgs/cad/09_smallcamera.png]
Small camera CAD


Notice how the original camera support is attached to the 3D printed support.

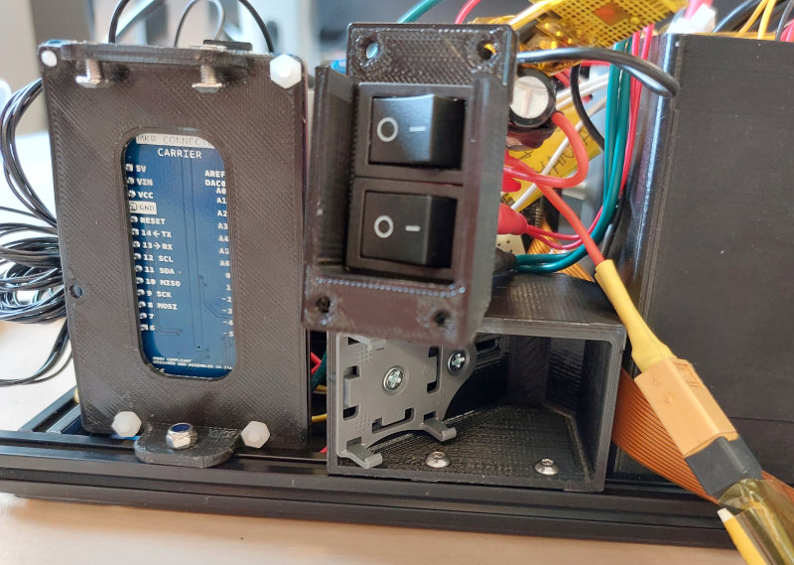
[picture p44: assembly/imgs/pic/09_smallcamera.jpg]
Small camera picture


---

## Attach the Cielo panel

Now that we have all the elements attached to the bottom, we are going to attach the Cielo panel.

First we have to attach the 80mm profile on Top. Make sure that it is oriented properly, with the 3 sliding nuts pointing to Cielo and 2 sliding nuts pointing to Top. Ideally, there would be silicone to prevent them from sliding.

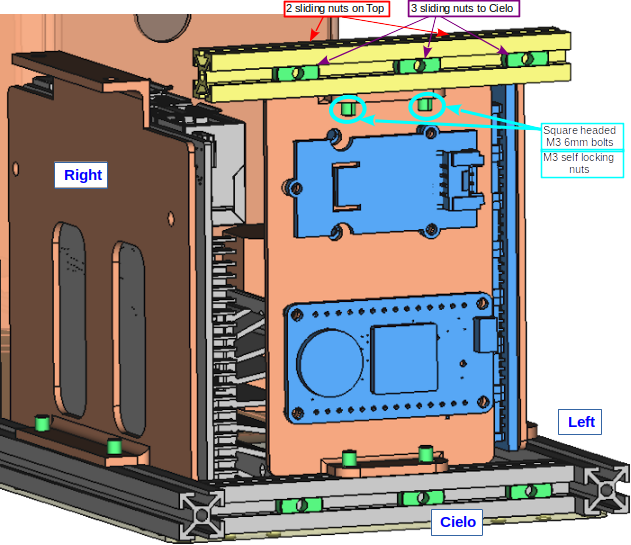
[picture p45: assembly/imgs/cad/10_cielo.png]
Cielo 1 CAD


Picture of the first step to attach the Cielo panel. Notice the silicone on the side of the Cielo nuts to prevent the nuts from sliding.

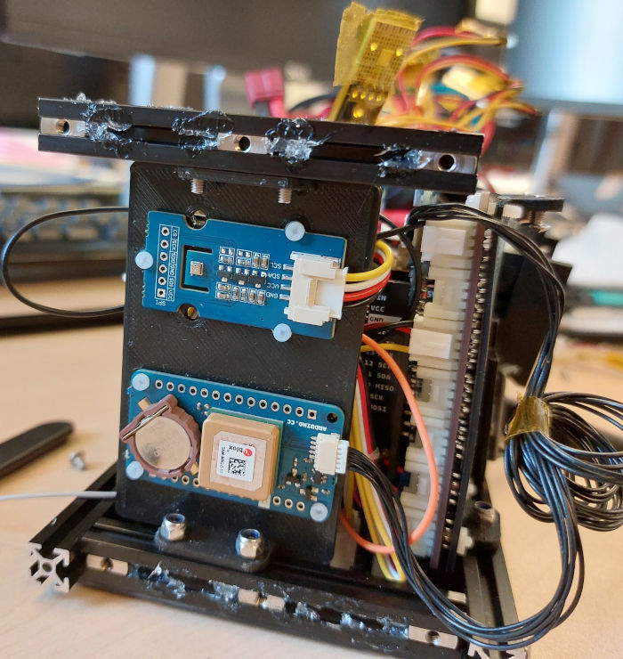
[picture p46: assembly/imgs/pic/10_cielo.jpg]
Cielo 1 picture


Include the self locking M3 nuts, but don't tighten them too much yet.

Now position the sensors support on the exact position you want it (by sliding a little bit right or left), and tighten the self locking nuts at the bottom.

Now set the Cielo plate with the two vertical 80mm profiles. Using the M3 4mm-socket button bolts and the sliding nuts. Do not tighten them too much because you will probably need to adjust them.

For the adjustment, you may need to move the top 80mm profile, to center it. Once you have adjusted the bolts by placing in its position, take the plate out and adjust the top self locking nuts of the sensors support.

Once it is all set, put back the plate and tighten all the socket button bolts of the Cielo plate.

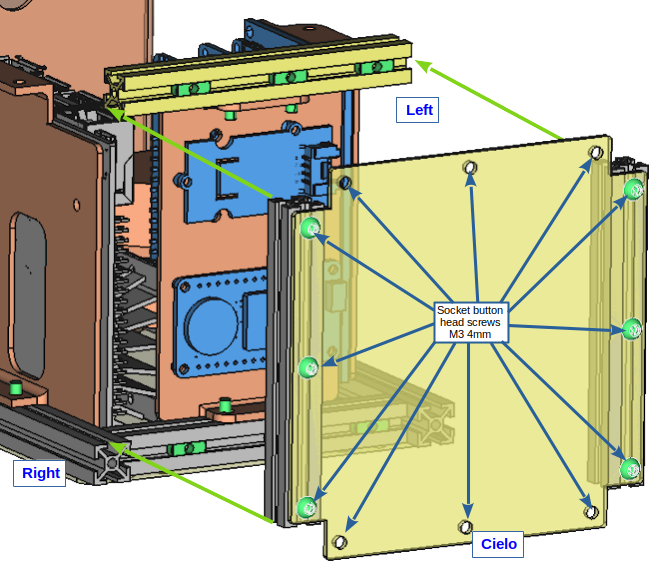
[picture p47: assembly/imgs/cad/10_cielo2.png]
Cielo 2 CAD


Picture with the plate before screwing the top and bottom socket button bolts

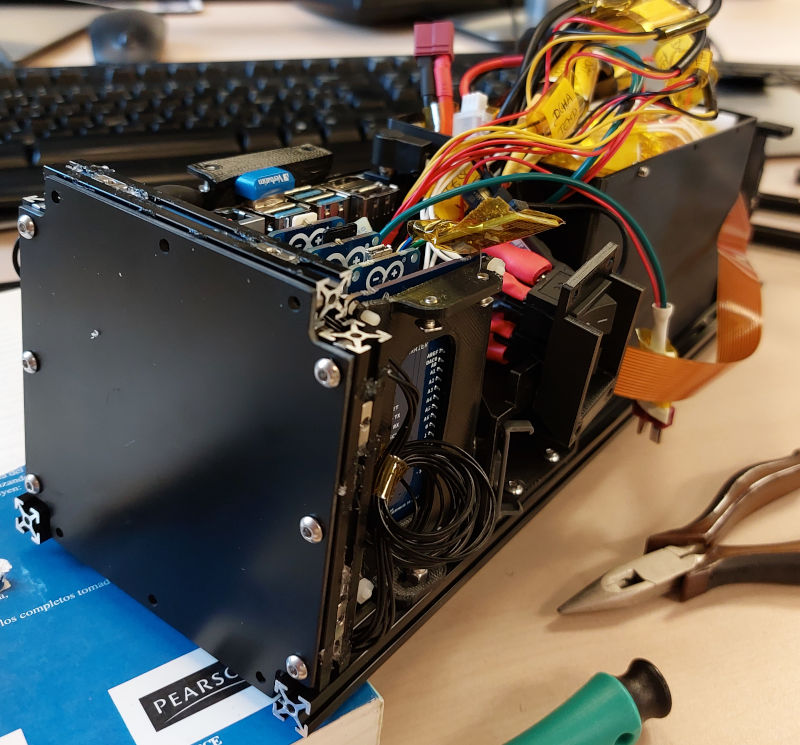
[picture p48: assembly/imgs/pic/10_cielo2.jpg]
Cielo 2 picture


---

## Set the antenna

The antenna can be placed outside over the Down plate, there is a hole for the cable, and some holes  that can be used to hold it with zip ties. However, since it can protrude more than what is allowed, we have decided to put it inside, between the Jetson Nano 3D support and the Right plate.

The [antenna](https://store.arduino.cc/products/dipole-pentaband-waterproof-antenna) has an adhesive tape, nevertheless it is recommended to attach it with a zip tie, as shown in the next picture.

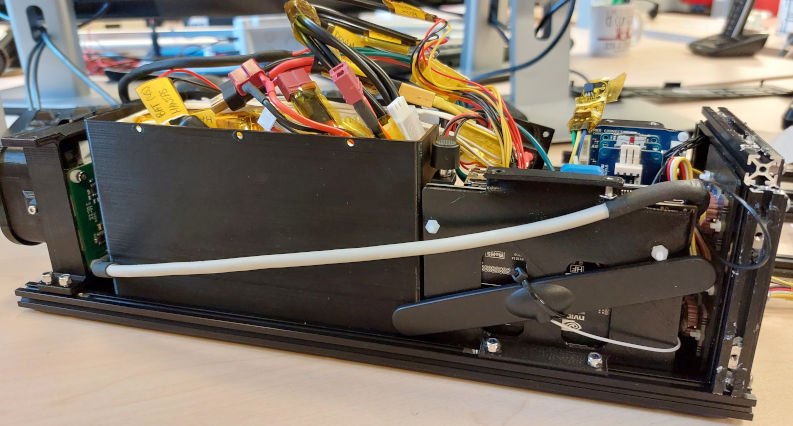
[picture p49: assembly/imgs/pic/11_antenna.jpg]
Antenna picture


---

## Secure the battery box

The battery box has holes on top to secure it, but in addition, you can include one or two [right angle brackets](https://www.makerbeam.com/makerbeam-right-angle-brackets-12p.html) to hold it.
In case you put two, put them at each side.

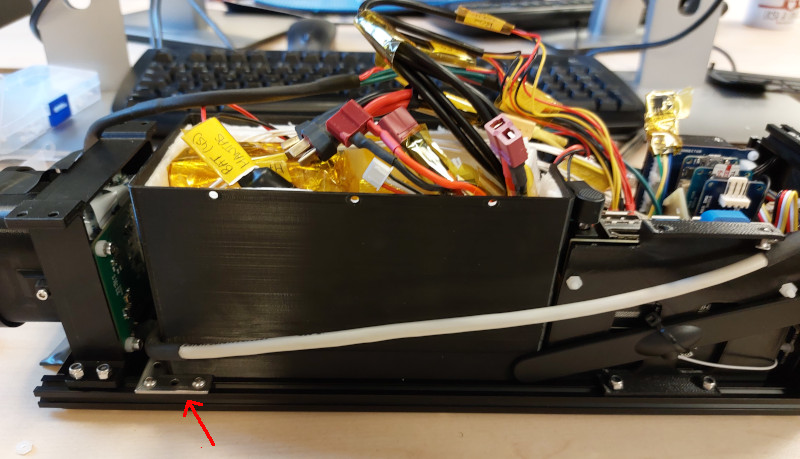
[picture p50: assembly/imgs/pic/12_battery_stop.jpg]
Battery stop


---

## Attach the Tierra panel

In a similar way to the Cielo panel, put the Tierra panel.

This panel is easier because it has not any support board attached, therefore you can mount the panel with the three 80mm profiles (Left, Top and Right) and attach it to the bottom 80mm profile.

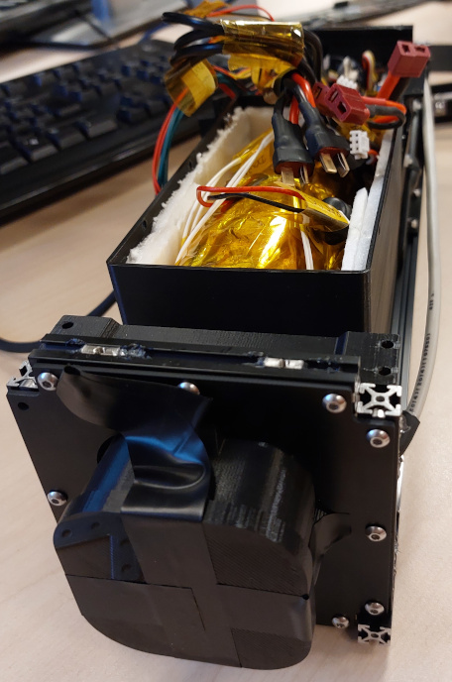
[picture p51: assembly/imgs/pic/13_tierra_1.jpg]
Tierra panel 1


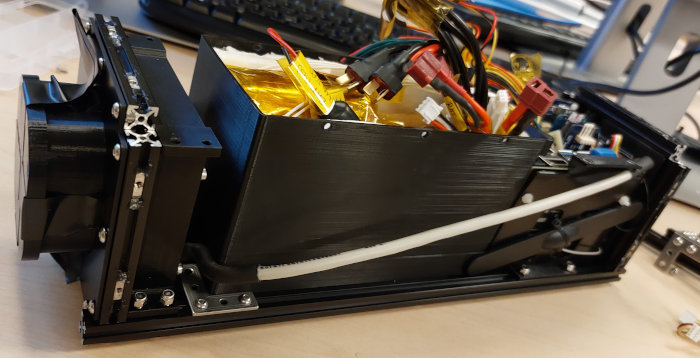
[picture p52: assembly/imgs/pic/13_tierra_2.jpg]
Tierra panel 2


---

## Assemble the Top-Right 340.5mm profile

Insert two M3 6mm square headed bolts and tow M3 12mm square headed bolts to attach the top of the Jetson Nano support and the top-right side of the camera, respectively.

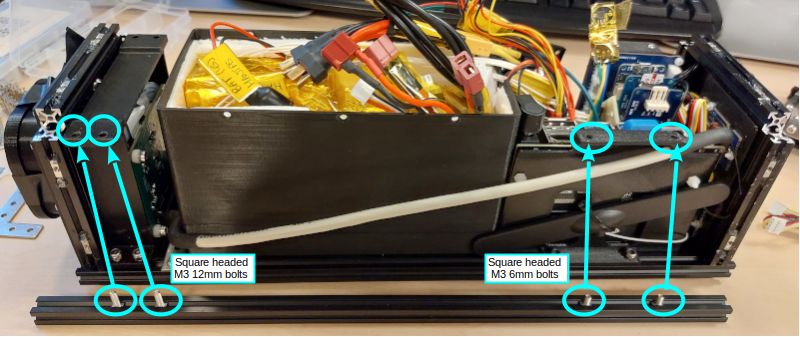
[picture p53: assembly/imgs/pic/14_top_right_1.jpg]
Top-right profile


Put the profile in its place, passing the bolts through the camera support:

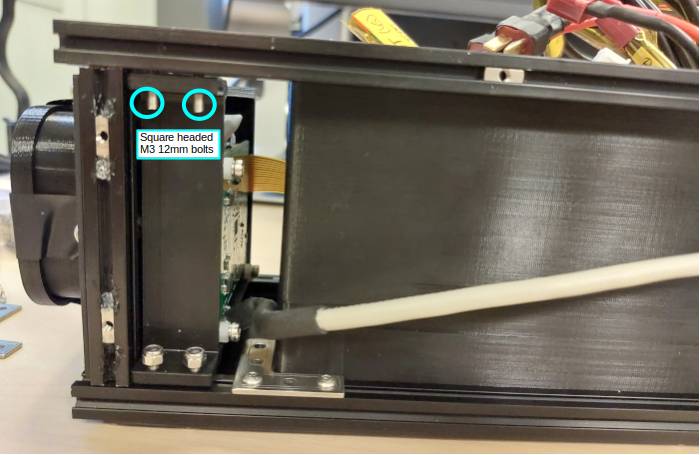
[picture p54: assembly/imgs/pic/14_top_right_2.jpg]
Top-right profile 2


And the Jetson Nano support:

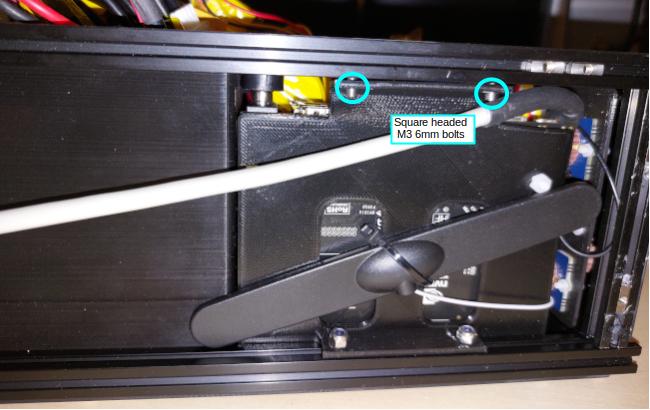
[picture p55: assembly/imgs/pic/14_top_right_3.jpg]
Top-right profile 3


Before tightening the bolts with self locking nuts, make sure that the Top profile is aligned with the bottom, and it is placed symmetrically, i.e. it has the same protrusion length in the Tierra direction  as in the Cielo direction.

Put the right plate on top to check if it is aligned. If it is aligned, tighten all the nuts.

Check if the sliding nuts inside the vertical 80mm profiles are aligned with the holes (thanks to the silicone), correct their position if they are not aligned.

---

## Assemble the Right panel

Put 10 sliding nuts with their M3 4mm socket button head bolts in the Right panel as shown in the picture. There are more holes that you can use, but with these is enough.

Leave the nuts loose, just enough to keep them with the bolt.

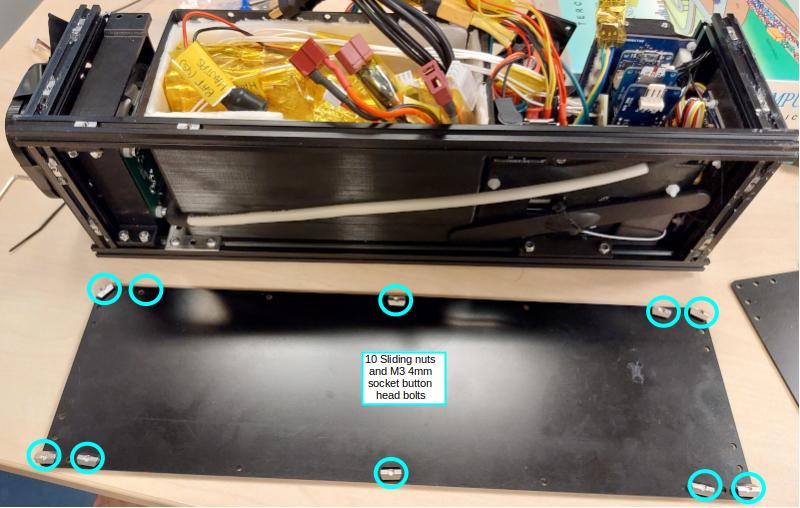
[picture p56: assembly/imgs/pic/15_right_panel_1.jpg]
Right panel 1


From one end, introduce the nuts in the profile slot and slide the panel until it is centered.

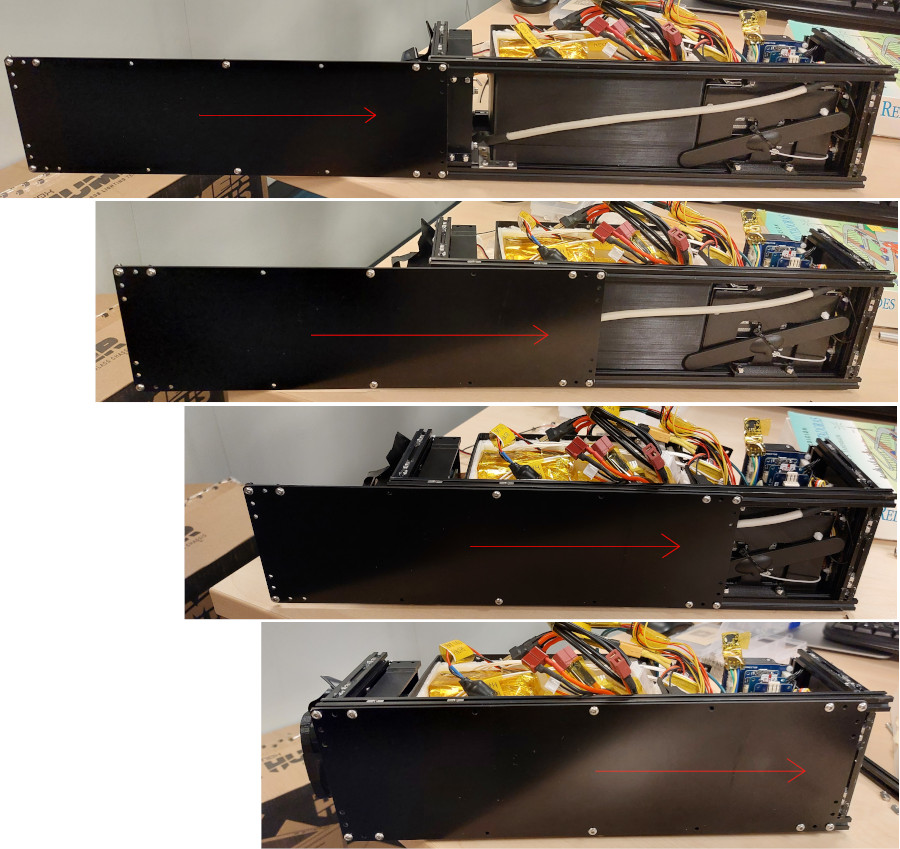
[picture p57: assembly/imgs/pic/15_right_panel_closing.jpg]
Right panel closing


Tighten all the bolts of the right panel:

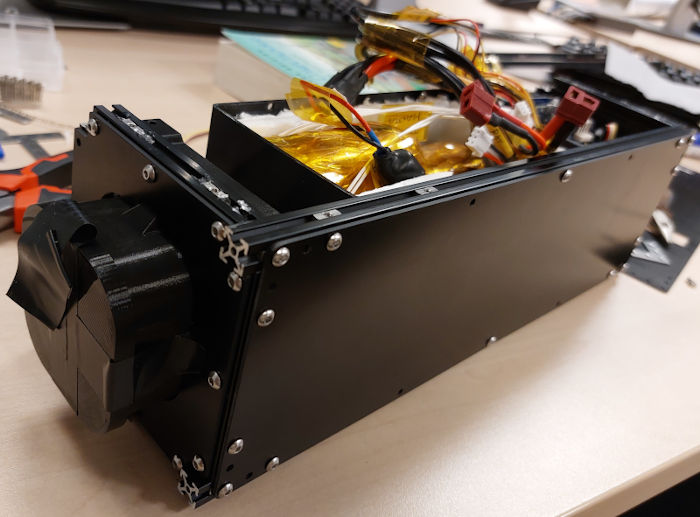
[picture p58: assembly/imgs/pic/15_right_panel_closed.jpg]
Right panel closed


---

## Adjust battery box

Adjust all elements inside, making sure that there is room for everything, and attach it to the profile with three M3 4mm socket button head bolts and sliding nuts.

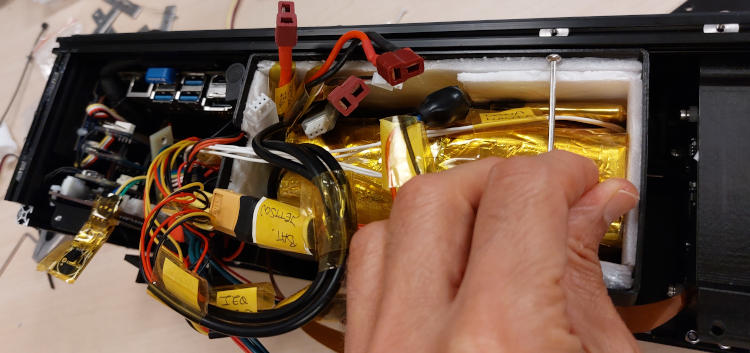
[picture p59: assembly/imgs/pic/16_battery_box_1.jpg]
Battery box bolt


The sliding nuts can be introduced from one end, and pushed until they are aligned with the battery box holes.

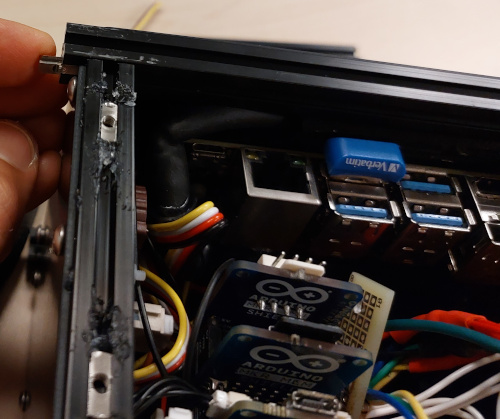
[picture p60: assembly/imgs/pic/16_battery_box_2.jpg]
Battery box bolt


---

## Assemble the Top-Left 340.5mm profile

This is similar to the Top-Right profile.

Using two M3 6mm square headed bolts and tow M3 12mm square headed bolts to attach the top of the Jetson Nano support and the top-right side of the camera, respectively.

Alternatively, as shown in the picture, you can use sliding nuts and blots.

Do the same as in the Top-Right, making sure everything is aligned. Superimpose the plate to check the alignment.

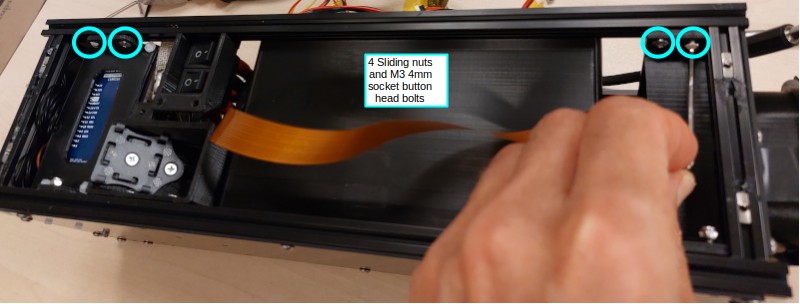
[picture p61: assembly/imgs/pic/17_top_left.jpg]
Top-left profile


Once it is aligned, tighten the bolts, and also secure this side of the battery box, as it was done before on the right side.

---

## Fix the switches and MOSFET board

Place the [switches 3D printed support](../cad/stl/switch_support.stl) and the MOSFET board on the Top-Left profile, using sliding nuts and M3 4mm socket button head bolts.
Check that the switches are aligned with the plate holes.

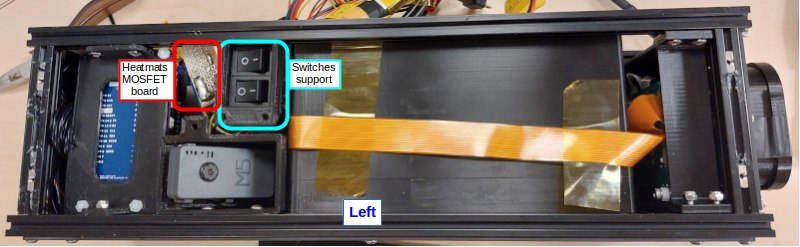
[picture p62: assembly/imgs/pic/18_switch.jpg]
Switchs and MOSFET board


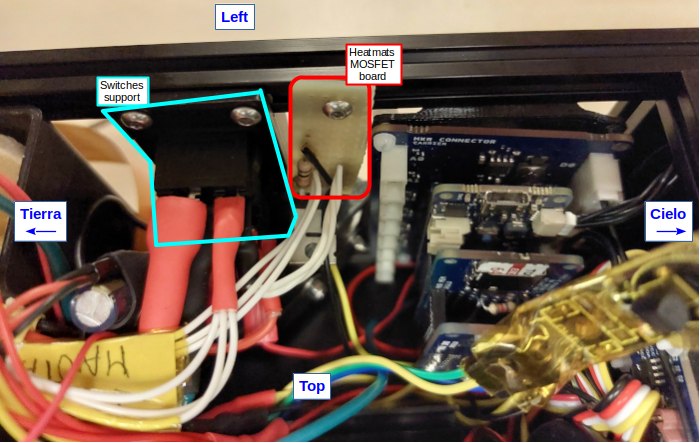
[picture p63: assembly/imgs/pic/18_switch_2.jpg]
Switchs and MOSFET board 2


---
## Assemble the Left panel

Do the same as in the right panel.
We have included two additional bolts, for the holes near the camera and switches.

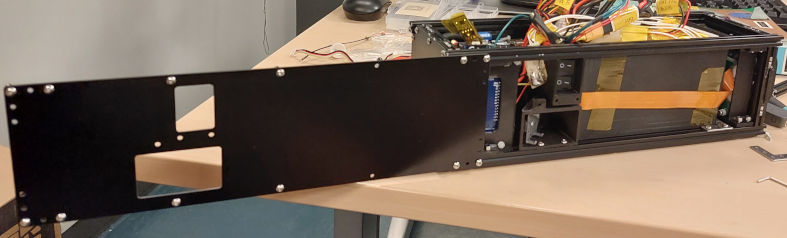
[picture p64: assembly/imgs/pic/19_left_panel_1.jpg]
Left panel 1


Left panel 2

Tighten the bolts and place the small camera:

Left panel 3

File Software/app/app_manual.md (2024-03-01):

#  Aplicación de Visualización de datos del Bentayga

Este manual te guiará a través de los pasos necesarios para ejecutar la aplicación de visualización de datos del CubeSat en tu sistema. La aplicación está escrita en Python y utiliza algunas bibliotecas específicas, por lo que debes asegurarte de que todo esté configurado correctamente.

## Requisitos Previos

Asegúrate de tener lo siguiente instalado en tu sistema:

1. **Python:** La aplicación está escrita en Python, así que necesitas tener Python instalado. Puedes descargar Python desde [python.org](https://www.python.org/downloads/) y seguir las instrucciones de instalación para tu sistema operativo.

2. **PyQt5:** La aplicación utiliza PyQt5 para la interfaz gráfica. Puedes instalarlo utilizando pip:

```sh
pip install PyQt5
```

3. **PyQtGraph:** PyQtGraph se utiliza para crear gráficos en tiempo real en la aplicación. Instálalo con pip:

```sh
pip install pyqtgraph
```
4. **NumPy:**  se utiliza para manipulación de matrices. Si aún no lo tienes instalado, puedes hacerlo con pip:

```sh
pip install numpy
```
## Ejecución de la Aplicación
Una vez que hayas configurado los requisitos previos, sigue estos pasos para ejecutar la aplicación:

1. **Clona el Repositorio:**

Clona el repositorio de la aplicación desde GitHub o descárgalo como un archivo ZIP y descomprímelo en tu sistema si aun no lo tienes descargado.

```sh
git clone https://github.com/alepape1/Bentayga-satellite.git
```

2. **Navega al Directorio de la Aplicación:**

Abre una terminal y navega al directorio donde se encuentra la aplicación. Por ejemplo:

3. **Ejecuta la Aplicación:**

Ejecuta la aplicación utilizando Python 3.7 o superior, tendrás que tener todas las dependencias anteriores instaladas:

```sh
python app.py
```

4. **Interactúa con la Aplicación:**

La aplicación se abrirá y mostrará gráficos en tiempo real de los datos del CubeSat.
Puedes ver la información actualizada en los gráficos y las etiquetas de la interfaz.
Cerrar la Aplicación:

Para cerrar la aplicación, simplemente cierra la ventana de la aplicación.
Registro de Datos
La aplicación registrará los datos en un archivo CSV en un directorio llamado "log" dentro del directorio de la aplicación. Los archivos CSV se nombrarán con la fecha y hora en que se inició la aplicación.

**Notas Importantes:**
Asegúrate de que la configuración del puerto COM (por ejemplo, COM25) y la velocidad de baudios (115200) en el código de la aplicación coincidan con la configuración de tu CubeSat.
Si encuentras problemas al ejecutar la aplicación, verifica que todos los paquetes necesarios estén instalados correctamente y que el archivo de código fuente de la aplicación tenga el nombre correcto.

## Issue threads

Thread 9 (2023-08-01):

CAD for cubesat, 3D parts + FR4 plates

felipe-m, 2023-08-01:
Make the CAD for the 3D parts, the laser cut fiber glass plates (FR-4) and the whole system

felipe-m, 2023-08-04:
closed by #10

Closed 2023-08-04.

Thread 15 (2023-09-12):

GPS through serial port

felipe-m, 2023-09-12:
Maybe the I2C has too many sensors

felipe-m, 2023-09-12:
The GPS shield needs pines D14, D13 and D7, in this case, the D7 of the Jetson nano pin 18 (orange) should be changed to D3
https://docs.arduino.cc/hardware/mkr-gps-shield

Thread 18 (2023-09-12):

Avoid the use of String

felipe-m, 2023-09-12:
It is not recommended:
https://hackingmajenkoblog.wordpress.com/2016/02/04/the-evils-of-arduino-strings/
https://forum.arduino.cc/t/understanding-the-evil-string/427528/12

felipe-m, 2023-09-16:
closed by #23

Closed 2023-09-16.

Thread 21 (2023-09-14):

Change pin 7 from Jetson to pin 3

felipe-m, 2023-09-14:
To avoid conflicts with Arduino MKR GPS

felipe-m, 2023-09-16:
closed by #22

Closed 2023-09-16.

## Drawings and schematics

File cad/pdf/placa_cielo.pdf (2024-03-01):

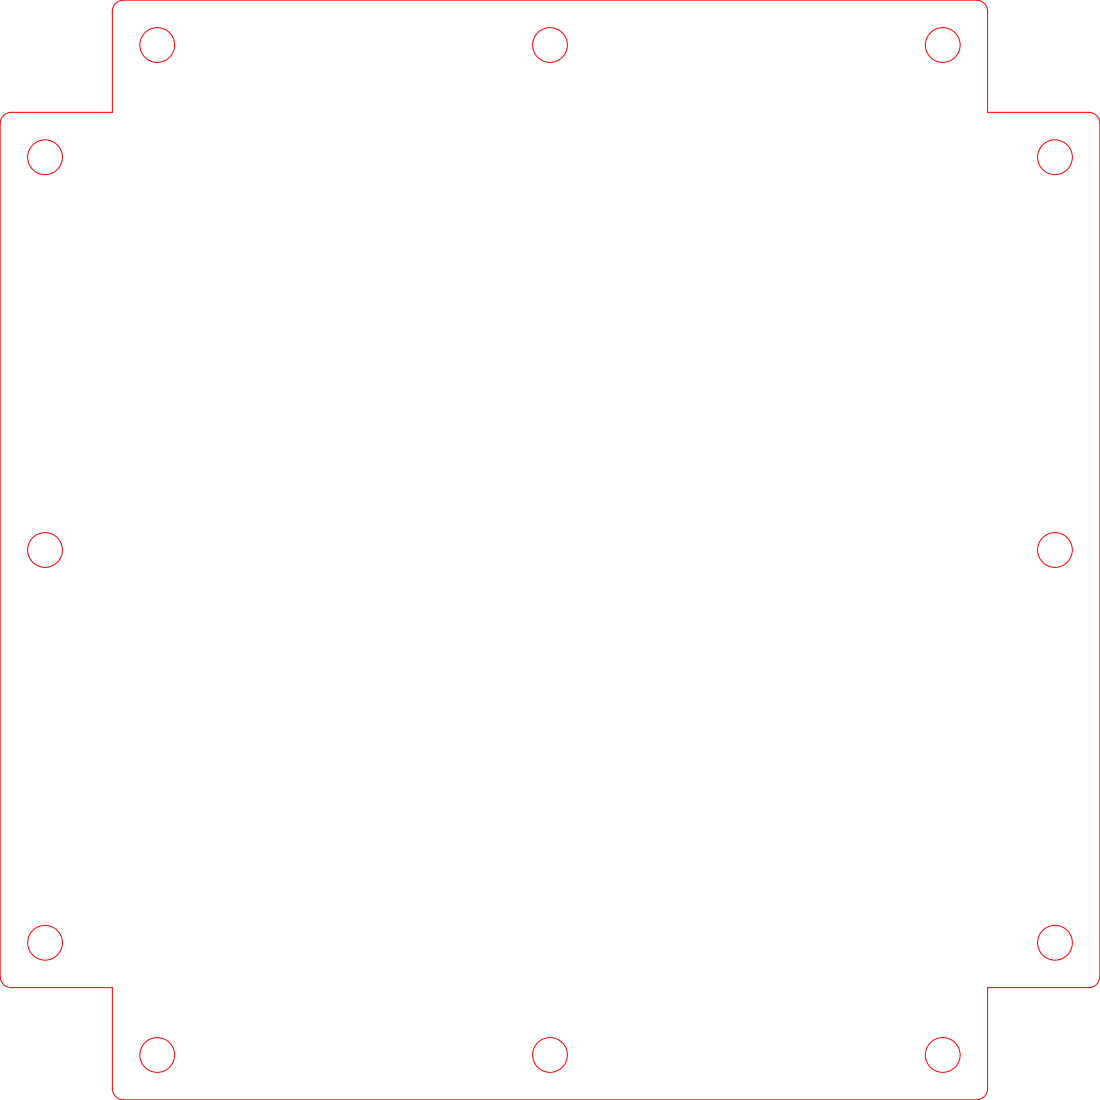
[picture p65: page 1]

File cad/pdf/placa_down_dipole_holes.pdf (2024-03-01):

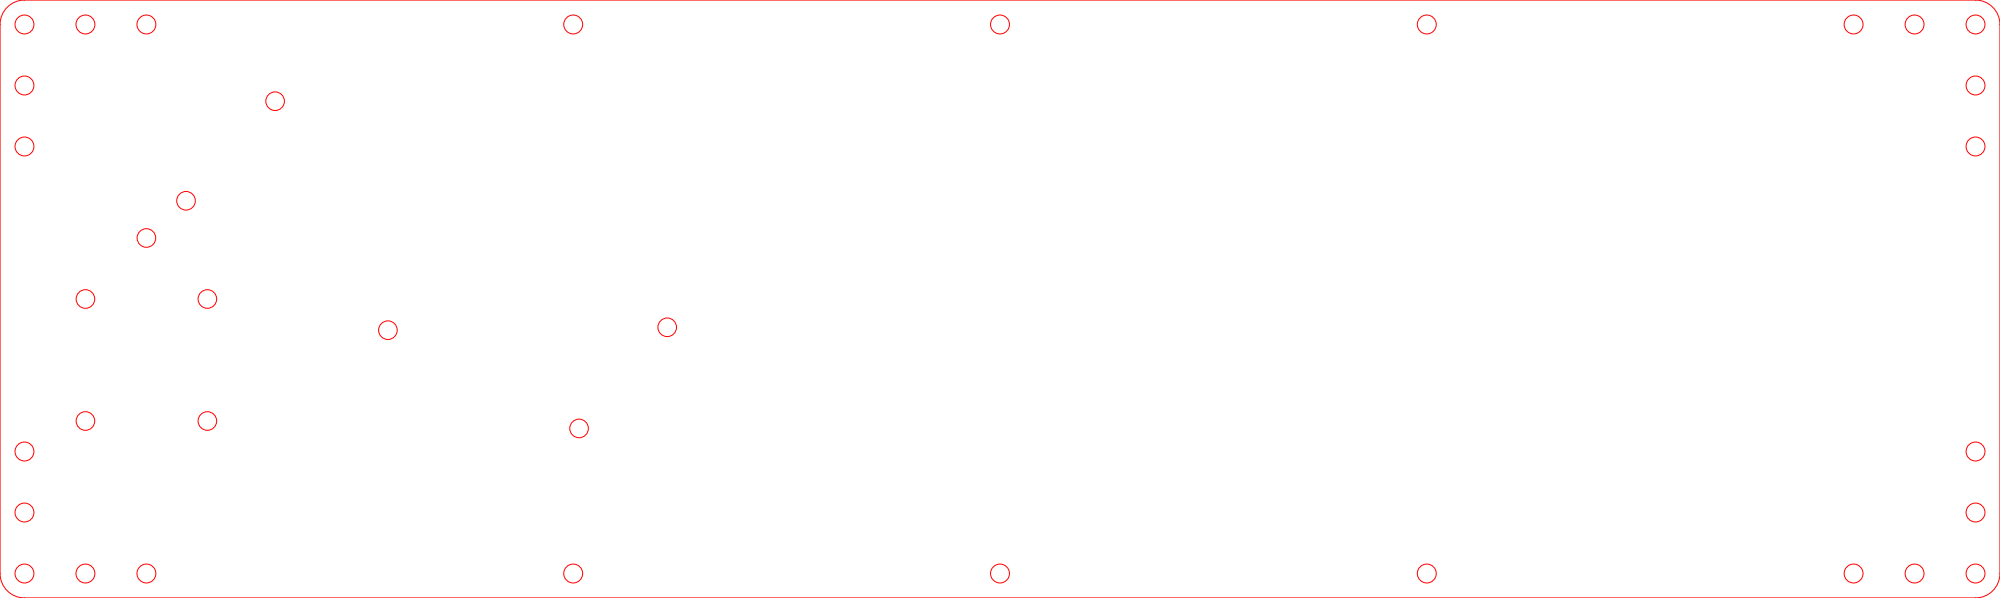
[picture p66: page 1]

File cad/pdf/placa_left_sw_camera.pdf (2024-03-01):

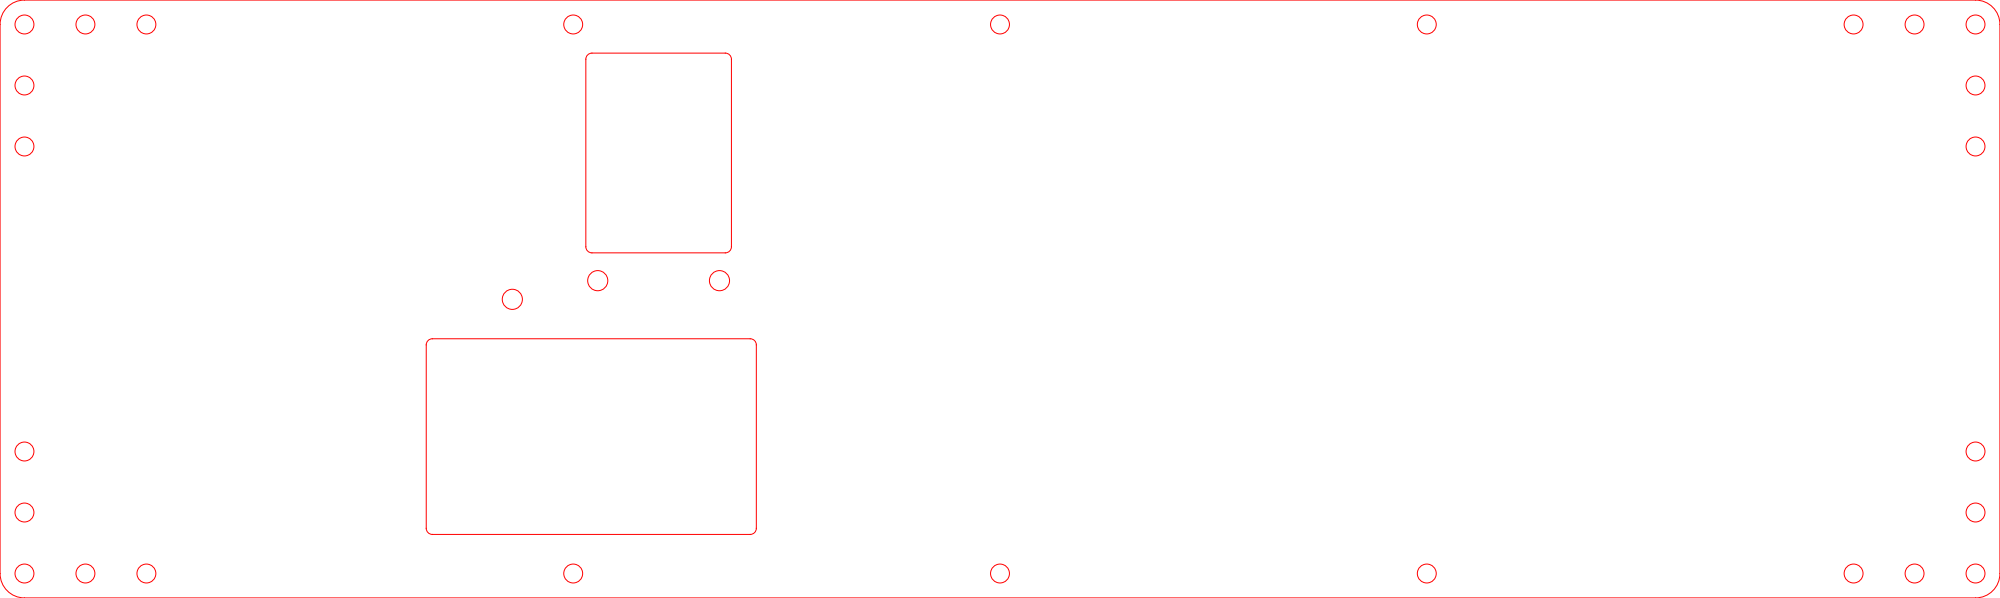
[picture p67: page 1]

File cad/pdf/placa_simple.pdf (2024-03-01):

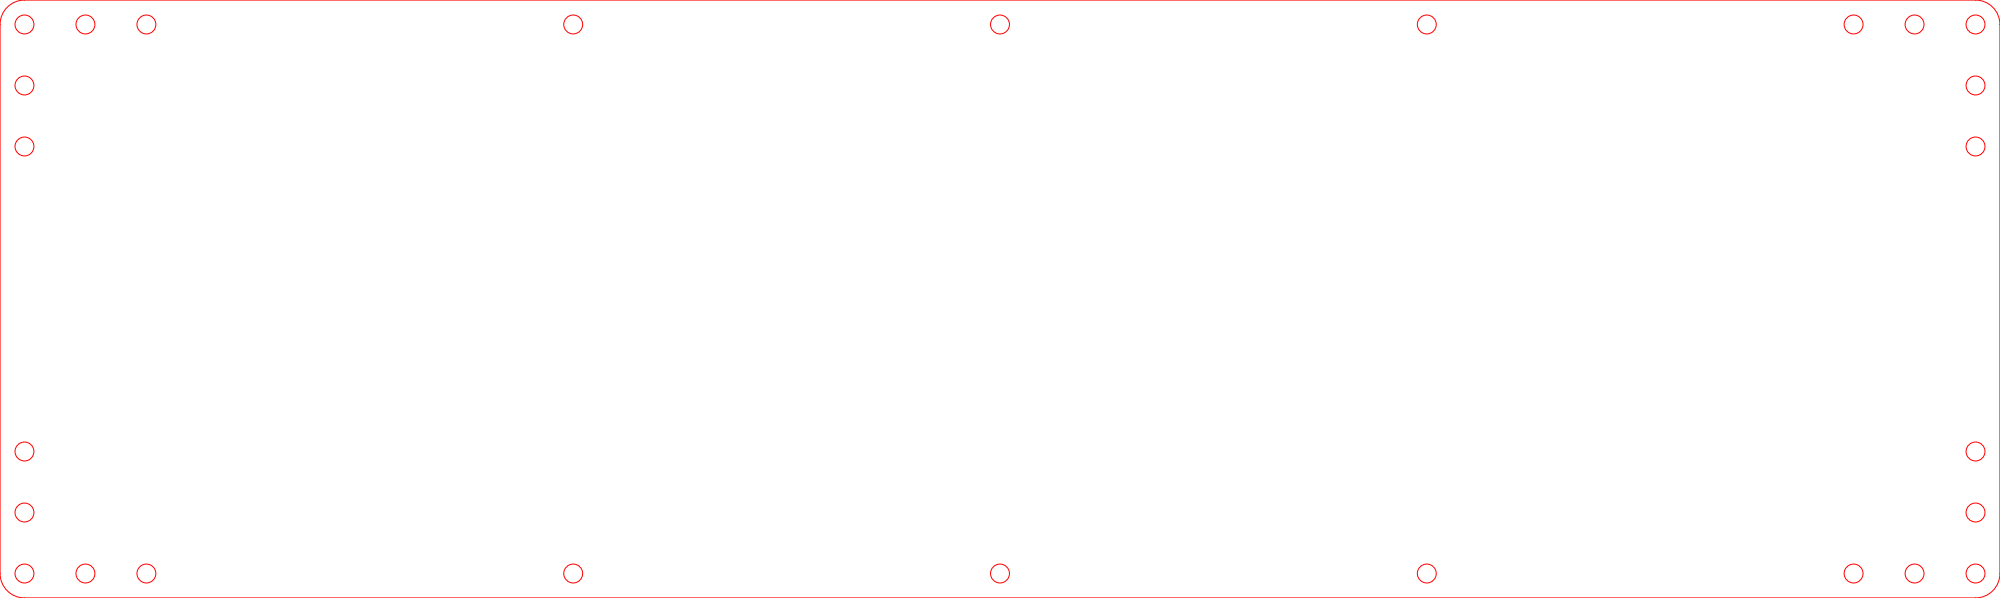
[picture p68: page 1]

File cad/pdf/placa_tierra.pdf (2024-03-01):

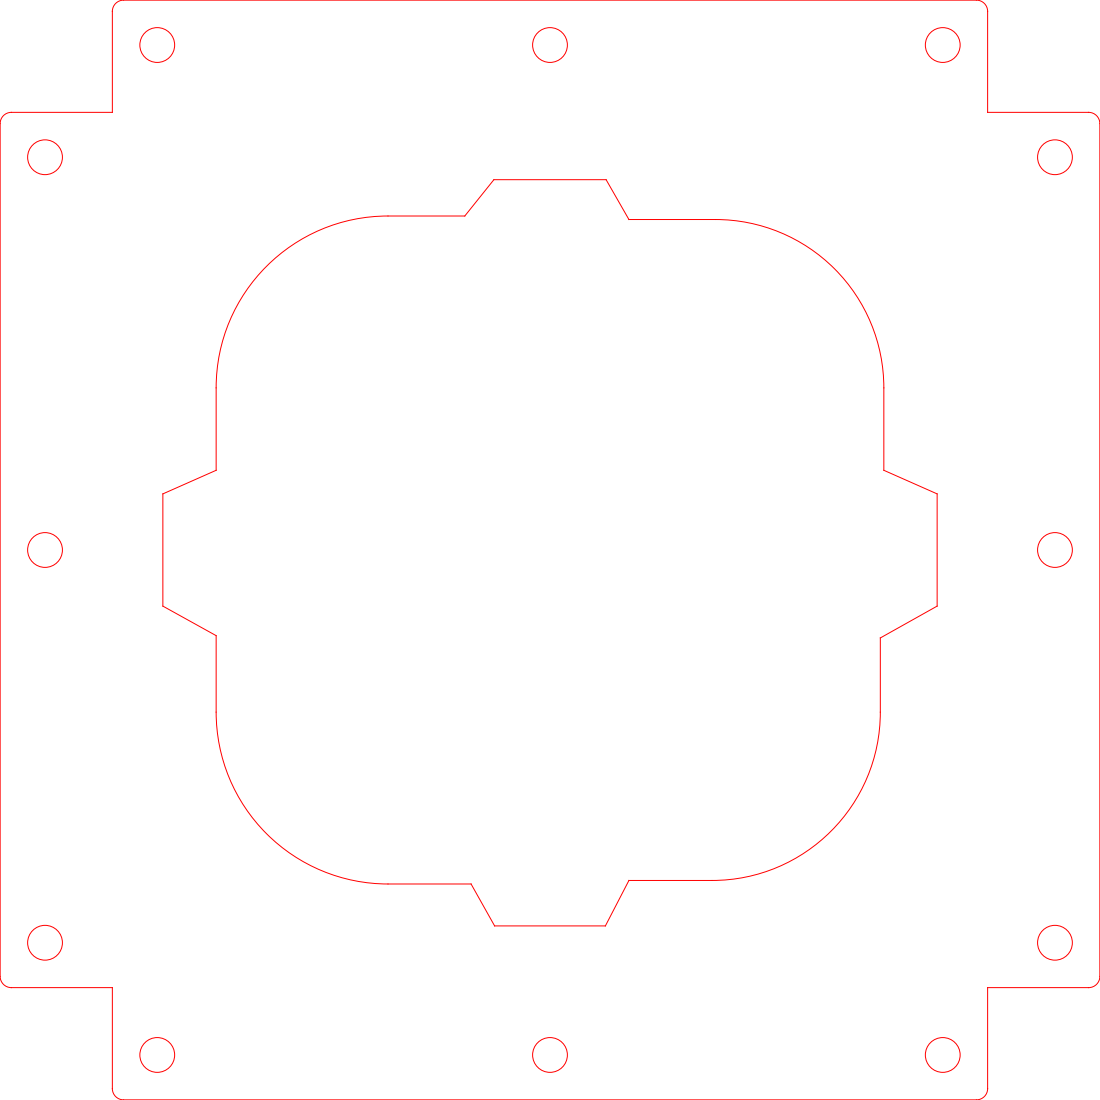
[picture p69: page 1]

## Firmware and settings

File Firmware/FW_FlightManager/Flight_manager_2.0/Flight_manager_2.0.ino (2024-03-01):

#include <Wire.h>
#include <Adafruit_Sensor.h>  // Adafruit Unified Sensor
#include <Adafruit_BNO055.h>
#include <Adafruit_BME280.h>
#include "DS1307.h"  // Grove RTC DS1307 - Seeed Studio
#include <LoRa.h> //  LoRa by Sandeep Mistry
#include <SparkFun_u-blox_GNSS_Arduino_Library.h>
#include <OneWire.h>
#include <DallasTemperature.h>
#include <SD.h>
#include <Adafruit_SleepyDog.h>
// #include "Arduino_CRC32.h"
// #include <PID_v1_bc.h>
#include <PID_v1.h>  // PID by Brett Beauregard
// #include <Arduino_MKRGPS.h>
// #include "ArduPID.h"

// COMMENT IN REAL MISSION
// UNCOMMENT FOR DEBUGGIN
//#define DEBUG

#ifdef DEBUG
  #define SERIAL_DEBUG(x) Serial.print (x)
  #define SERIAL_DEBUG_LN(x) Serial.println (x)
#else  // do not use serial print: do nothing:
  #define SERIAL_DEBUG(x)
  #define SERIAL_DEBUG_LN(x)
#endif

// -----------------------------------------
// COMMENT define IN REAL MISSION OR IF YOU DONT WANT TO TEST AVAILABLE SRAM
// UNCOMMENT define IF YOU WANT TO TEST AVAILABLE SRAM
#define CHECK_FREE_SRAM 

// You need to install https://github.com/mpflaga/Arduino-MemoryFree
#ifdef CHECK_FREE_SRAM
#include <MemoryFree.h>
#include <pgmStrToRAM.h>
#endif


// --------------------------------------------------------------------
// ---- CHANGE HERE THE BEHAVIOUR OF THE HEATPAD CONTROL WITH TEMPERATURE
// if you are testing at room temperature, outside a fridge
#define TESTING_ROOM_TEMP  // COMMENT IN REAL MISSION OR TESTING INSIDE A FREEZER

// Below this temperature the heatpad will be ON. Should be low
#ifdef TESTING_ROOM_TEMP
const int MIN_TEMP_START = 35;  // but this is for testing at room temperature
#else                           // Real mission or inside a freezer
const int MIN_TEMP_START = 5;  // Below 5 the heatpad will be on
#endif


#define SAMPLE_SENSOR_TIME 100
#define SAMPLE_GPS_TIME 6000
#define SEND_DATA_DELAY 1000
#define WRITE_SD_DATA_DELAY 2000
#define WATCHDOG_TIMEOUT 20000

#define fileLog "tLog.txt"  //Less 8 character plus extension (.txt) for the file name
// if any sensor is above this is the temperature, heatmats should be off
//const int LIMIT_TEMP_HIGH = 45;

const int TEMP_STEP = 5;  // Temperature steps that define the levels
// Half way between the starting temperature and the extreme
const int MIN_TEMP_2 = MIN_TEMP_START - TEMP_STEP;  // More levels could be added
const int MIN_TEMP_3 = MIN_TEMP_2 - TEMP_STEP;      // More levels could be added
// If this low temperature is reached, the heatpads will be at maximum temperature
const int MIN_TEMP_EXTREM = MIN_TEMP_3 - TEMP_STEP;  // More levels could be added
// We have defined 4 levels
//                   Mission/Freezer  -- Room temperature experiment
// MIN_TEMP_START  =   5 C                40   -- below this, heatpad are partially ON
// MIN_TEMP_2      =   0 C                35
// MIN_TEMP_3      =  -5 C                30
// MIN_TEMP_EXTREM = -10 C                25   -- below this, heatpads are FULL-ON

// There are 5 DS18B20 temperature sensors and another one of a different kind
//
// The temperature sensors inside the battery box should have a similar temperature
// Especially the 3 sensors inside the mats
// If one of them is off, it should be discarded. Double check with the other sensor
// inside the box.
// This will be the maximum allowable temperature difference.
// change it if it is too high or low
// This is for the difference with 3 the sensor temperatures, comparing the temperature of the
// middle with the other two. If any is higher than this difference, it could be a problem in a sensor
const int MAX_DIFF_SENS_TEMP = 5;  // if sensors temperature is larger than this, it might be a problem



// --------- END OF TEMPERATURE TESTING CHANGES -----------------------------------

// Since the heatpads are rated for 12V and their batteries are 14.4V,
// The maximum value for the PWM should be 212 = 255*12/14.4

const int HEAT_FULL = 170;
const int HEAT_START = (int)HEAT_FULL / 4;      // 53
const int HEAT_2 = (int)HEAT_FULL / 2;          // 106
const int HEAT_3 = (int)((3 * HEAT_FULL) / 4);  // 159
const int MAX_OUTPUT_PWM = 220;



// Pin were the PWM output to the MOSFET for the heatmats:
const int PIN_HEATMATS = 1;  // cannot be 0, because it is used by the IMU

// Pin were the 1-Wire bus with the temp sensors DS18B20
const int PIN_ONEWIRE = 2;

//Information camera capturing and memory size available
const int GPIO_C = 5;    // GPIO pin for the camera capturing signal
const int GPIO_LSB = 6;  // GPIO pin for the less significative bit of the memory capacity signal
const int GPIO_MSB = 3;  // GPIO pin for the less significative bit of the memory capacity signal. CHANGED, before was pin 7, but there was conflict


// These are the address of the 5 DS18B20 temperature sensors, their code has been requested
// with the sketch: detect_ds1820_tempsens_id.ino
DeviceAddress TEMP_CUBESAT_ADDR = { 0x28, 0xFF, 0x10, 0x4B, 0x20, 0x18, 0x01, 0x10 };    // inside cubesat
DeviceAddress TEMP_BAT_BOX_ADDR = { 0x28, 0x55, 0xB3, 0x95, 0xF0, 0x01, 0x3C, 0xEE };    // inside battery box
DeviceAddress TEMP_BAT_LEFT_ADDR = { 0x28, 0x37, 0x50, 0x95, 0xF0, 0x01, 0x3C, 0xD7 };   // inside battery box, in left heatmat
DeviceAddress TEMP_BAT_RIGHT_ADDR = { 0x28, 0x53, 0x6E, 0x95, 0xF0, 0x01, 0x3C, 0xEE };  // inside battery box, in right heatmat
DeviceAddress TEMP_BAT_DOWN_ADDR = { 0x28, 0x7A, 0xEF, 0x95, 0xF0, 0x01, 0x3C, 0xC8 };   // inside battery box, in bottom heatmat
char DS18_NR = 5;                                                                        // Number of DS18 sensors
// variables that check if the DS18B20 temperature sensors have been found
bool temp_cubesat_found = false;
bool temp_bat_box_found = false;
bool temp_bat_left_found = false;
bool temp_bat_right_found = false;
bool temp_bat_down_found = false;



// Resolution can be 9,10,11,12, the higher the slower
// default seems to be the last that has been set.
// with  9 it seems that it is 0.50 C resolution
// with 10 it seems that it is 0.25 C resolution
const uint8_t SENSOR_BIT_RESOL = 11;

// Instance to classes OneWire y DallasTemperature
OneWire OneWireObj(PIN_ONEWIRE);
DallasTemperature sensor_DS18(&OneWireObj);

// ArduPID myController;

Adafruit_BNO055 bno = Adafruit_BNO055(55, 0x28, &Wire);
Adafruit_BME280 bme;

SFE_UBLOX_GNSS myGNSS;
DS1307 clock;  //define a object of DS1307 class

// Arduino_CRC32 crc32;

struct SensorData {

  float roll;
  float pitch;
  float heading;
  // 5 DS18B20 temp sensors
  float battTempLeft;     // Temperature of batteries inside heatmat, at the left, looking from the camera
  float battTempRight;    // Temperature of batteries inside heatmat, at the right, looking from the camera
  float battTempDown;     // Temperature of batteries inside heatmat, at the bottom, opposite to the battery box openning
  float battTempBox;      // Temperature of batteries inside the box, outside the heatmats
  float TempCubesatDS18;  // Temperature of the cubesat, taken from the DS18B20 sensor
  // the other temperature sensor, not DS18B20
  float temperature;
  float pressure;
  float humidity;
  float GpsAltitude;
  float latitude;
  float longitude;
  float speed;
  uint8_t numSatellites;
  uint16_t year;
  uint8_t month;
  uint8_t day;
  uint8_t hour;
  uint8_t minute;
  uint8_t second;
  uint8_t camera_info; // info of Camera Flag (bit2), and Jetson memory usage (bits 1 and 0)
  uint8_t camera_flag; // Remove when ground station is updated
  // uint32_t checksum;
};


SensorData sensorData;

// Archivo en la tarjeta SD
File dataFile;

// dataFile = SD.open(fileLog, FILE_WRITE);

// Definir el contador para el sampling del barometro , IMU y sensores de temperatura
uint32_t sample_counter = 0;

//Definir el contador para el sampling del GPS
uint32_t GPS_sample_counter = 0;

// Definir el contador para el envio de datos
uint32_t send_data_timer = 0;

// Definir el contador de tiempo para la escritura en la SD de la trama de datos
uint32_t write_sd_data_timer = 0;

bool update_time = true;

File openDataFile(const char *filename);

void saveDataToSDCard(File dataFile, SensorData &sensorData);
bool temperature_sensor_init();
void IMU_calibration();
void IMU_get_values(SensorData &sensorData);
void print_dev_addr(DeviceAddress addr);
bool comp_dev_addr(DeviceAddress addr1, DeviceAddress addr2);
int temp_ctrl(int temp_left, int temp_down, int temp_right);

// Constantes de configuración del PID
double setpoint = 20.0;  // Temperatura deseada en grados Celsius
double kp = 0.9;         // Coeficiente proporcional
double ki = 0.001;       // Coeficiente integral
double kd = 0.4;         // Coeficiente derivativo

//Define the aggressive and conservative Tuning Parameters
double aggKp = 4, aggKi = 0.2, aggKd = 1;
double consKp = 1, consKi = 0.05, consKd = 0.25;

// Variables globales para el controlador PID
double input, output;

//Specify the links and initial tuning parameters
PID myPID(&input, &output, &setpoint, consKp, consKi, consKd, DIRECT);



void setup() {

  Watchdog.disable();
#ifdef DEBUG
  Serial.begin(115200);
#endif
  delay(2000);

  //GPIO configuration for camera info flags
  pinMode(GPIO_C, INPUT_PULLUP);
  pinMode(GPIO_LSB, INPUT_PULLUP);
  pinMode(GPIO_MSB, INPUT_PULLUP);


  // Setup the output to control the heatpad, which goes to the MOSFET
  pinMode(PIN_HEATMATS, OUTPUT);    // it has to be a PWM pin
  digitalWrite(PIN_HEATMATS, LOW);  // turn-off the heatmats, until we have temperature values

  // Inicialización del controlador PID
  myPID.SetMode(AUTOMATIC);

  clock.begin();

  SERIAL_DEBUG_LN("Bentayga I. System init");

  temperature_sensor_init();  // Initializacion of the 5 DS18B20 temperature sensors

  // Inicializar la tarjeta SD
  if (!SD.begin(4)) {
    SERIAL_DEBUG_LN("ERROR: Failed to initialize SD card!");

  } else {

    SERIAL_DEBUG_LN("SD card initialized.      Status: OK");
    dataFile = openDataFile(fileLog);
    dataFile.println("Reset WatchDog");
    dataFile.close();
  }

  if (!bno.begin()) {
    SERIAL_DEBUG_LN("ERROR: BNO055 NOT detected");

  } else {
    SERIAL_DEBUG_LN("BNO55 IMU sensor connected.Status: OK");
    IMU_calibration();
  }

  //  if (!GPS.begin()) {
  //   SERIAL_DEBUG_LN("Failed to initialize GPS!");
  // } else {
  //   SERIAL_DEBUG_LN("GPS System init.          Status: OK");
  // }

  if (!myGNSS.begin()) {
    SERIAL_DEBUG_LN("Failed to initialize GPS!");
  } else {
    SERIAL_DEBUG_LN("GPS System init.          Status : OK");
  }

  if (!bme.begin(0x76)) {  // la dirección puede ser 0x77 dependiendo de tu módulo
    SERIAL_DEBUG_LN("ERROR: Failed to initialize the barometer BME280");
  } else {
    SERIAL_DEBUG_LN("BME280 Sensor.            Status: OK");
  }

  if (!LoRa.begin(868E6)) {
    SERIAL_DEBUG_LN("ERROR: Starting LoRa failed!");
  } else {
    SERIAL_DEBUG_LN("LoRa Transceiver.         Status: OK");
  }

  LoRa.setTxPower(20);
  LoRa.setSpreadingFactor(12);

  delay(4000);

  //Watchdog.enable for the setup and loop
  Watchdog.enable(WATCHDOG_TIMEOUT);

  sample_counter = millis();
}

void loop() {

  IMU_get_values(sensorData);

  // if (millis() - sample_counter >= SAMPLE_SENSOR_TIME) {

#ifdef CHECK_FREE_SRAM
  // Check free memory:
  SERIAL_DEBUG("Free Memory: ");
  SERIAL_DEBUG_LN(freeMemory());
#endif

  // Abrir el archivo en modo de escritura
  SERIAL_DEBUG_LN("Before barometer measure");
  sensorData.temperature = bme.readTemperature();
  sensorData.humidity = bme.readHumidity();
  sensorData.pressure = bme.readPressure() / 100.0;
  sensor_DS18.requestTemperatures();  //Se envia el comando para leer la temperatura

  // Reading the 5 DS18B20 sensors
  sensorData.TempCubesatDS18 = sensor_DS18.getTempC(TEMP_CUBESAT_ADDR);
  sensorData.battTempBox = sensor_DS18.getTempC(TEMP_BAT_BOX_ADDR);
  sensorData.battTempLeft = sensor_DS18.getTempC(TEMP_BAT_LEFT_ADDR);
  sensorData.battTempRight = sensor_DS18.getTempC(TEMP_BAT_RIGHT_ADDR);
  sensorData.battTempDown = sensor_DS18.getTempC(TEMP_BAT_DOWN_ADDR);

  // int temp_left = (int)round(sensorData.battTempLeft);
  // int temp_down = (int)round(sensorData.battTempDown);
  // int temp_right = (int)round(sensorData.battTempRight);
  // int temp_box = (int)round(sensorData.battTempBox);

  // heatmat temperature control
  temp_ctrl(sensorData.battTempLeft, sensorData.battTempDown, sensorData.battTempRight);


  // if(millis() - GPS_sample_counter >SAMPLE_GPS_TIME){

  //   SERIAL_DEBUG_LN("Before GPS measure");
  //   sensorData.latitude = GPS.latitude();
  //   sensorData.longitude = GPS.longitude();
  //   sensorData.GpsAltitude = GPS.altitude();
  //   sensorData.speed = GPS.speed();
  //   sensorData.numSatellites = GPS.satellites();
  //   }

  if(millis() - GPS_sample_counter >SAMPLE_GPS_TIME){
   SERIAL_DEBUG_LN("Before GPS measure");
   sensorData.latitude = myGNSS.getLatitude() / 10000000.0;
   sensorData.longitude = myGNSS.getLongitude() / 10000000.0;
   sensorData.GpsAltitude = myGNSS.getAltitude() / 1000.0;
   sensorData.speed = myGNSS.getGroundSpeed() / 1000.0;
   sensorData.numSatellites = myGNSS.getSIV();
   GPS_sample_counter = millis();
   delay(10);
  }

  sensorData.camera_info = get_camera_info();

  // sensorData.checksum = crc32.calc((uint8_t *)&sensorData, sizeof(sensorData) - sizeof(sensorData.checksum));

  // if (update_time) {
  //   if (myGNSS.getTimeValid()) {

  //     clock.fillByYMD(myGNSS.getYear(), myGNSS.getMonth(), myGNSS.getDay());      //Jan 19,2013
  //     clock.fillByHMS(myGNSS.getHour(), myGNSS.getMinute(), myGNSS.getSecond());  //15:28 30"
  //     // clock.fillDayOfWeek(SAT);//Saturday
  //     clock.setTime();  //write time to the RTC chip
  //     SERIAL_DEBUG_LN("TIME GPS SYNC OK");
  //     update_time = false;
  //   }
  // }

  //   sample_counter = millis();
  // }

  SERIAL_DEBUG_LN("Before clock get time");
  clock.getTime();
  sensorData.year = clock.year + 2000;
  sensorData.month = clock.month;
  sensorData.day = clock.dayOfMonth;
  sensorData.hour = clock.hour;
  sensorData.minute = clock.minute;
  sensorData.second = clock.second;


#ifdef DEBUG
  // string_data is sent to serial port
  String string_data = String(sensorData.day) + "/" + String(sensorData.month) + "/" + String(sensorData.year) + " " + String(sensorData.hour) + ":" + String(sensorData.minute) + ":" + String(sensorData.second) + "\t" + "Roll:" + String(sensorData.roll) + "\t" + "Pitch:" + String(sensorData.pitch) + "\t" + "Heading:" + String(sensorData.heading) + "\t" + "Temp-batt-Left:" + String(sensorData.battTempLeft) + "\t" + "Temp-batt-Right:" + String(sensorData.battTempRight) + "\t" + "Temp-batt-Down:" + String(sensorData.battTempDown) + "\t" + "Temp-batt-Box:" + String(sensorData.battTempBox) + "\t" + "Temp-Cubesat-DS18:" + String(sensorData.TempCubesatDS18) + "\n" + "Temperature:" + String(sensorData.temperature) + "\t" + "Humidity:" + String(sensorData.humidity) + "\t" + "Pressure:" + String(sensorData.pressure) + "\t" + "GpsAltitude:" + String(sensorData.GpsAltitude) + "\t" + "Latitude:" + String(sensorData.latitude, 6) + "\t" + "Longitude:" + String(sensorData.longitude, 6) + "\t" + "Speed:" + String(sensorData.speed) + "\t" + "NumSatellites:" + String(sensorData.numSatellites) + "\t" + "Camera:" + String(sensorData.camera_info) + "\t" + "Capturing:" + String(sensorData.camera_flag);
  //  + "," + "CheckSum:" + String(sensorData.checksum, HEX);
#endif

  if (millis() - send_data_timer >= SEND_DATA_DELAY) {

#ifdef DEBUG
    SERIAL_DEBUG_LN(string_data);
#endif
    packData_and_send(sensorData);
    send_data_timer = millis();
  }

  if (millis() - write_sd_data_timer >= WRITE_SD_DATA_DELAY) {

    SERIAL_DEBUG_LN("Before write SD");
    saveDataToSDCard(openDataFile(fileLog), sensorData);
    write_sd_data_timer = millis();
    delay(5);
  }

  Watchdog.reset();
}

// print a One Wire device address a DeviceAddress is a 8 byte array
void prnt_dev_addr(DeviceAddress addr) {
  for (uint8_t i = 0; i < 8; i++) {
    // If only one digit, fill it wit a zero on the left
    if (addr[i] < 16) SERIAL_DEBUG("0");
    // show in HEX
#ifdef DEBUG    
    Serial.print(addr[i], HEX);
#endif
 
  }
  SERIAL_DEBUG_LN("");
}

void packData_and_send(SensorData sensorData) {
  LoRa.beginPacket();
  LoRa.write((uint8_t *)&sensorData, sizeof(SensorData));
  LoRa.endPacket();
}

void IMU_get_values(SensorData &sensorData) {

  //could add VECTOR_ACCELEROMETER, VECTOR_MAGNETOMETER,VECTOR_GRAVITY...
  sensors_event_t orientationData, angVelocityData, linearAccelData, magnetometerData, accelerometerData, gravityData;

  bno.getEvent(&orientationData, Adafruit_BNO055::VECTOR_EULER);
  bno.getEvent(&angVelocityData, Adafruit_BNO055::VECTOR_GYROSCOPE);
  bno.getEvent(&linearAccelData, Adafruit_BNO055::VECTOR_LINEARACCEL);
  bno.getEvent(&magnetometerData, Adafruit_BNO055::VECTOR_MAGNETOMETER);
  bno.getEvent(&accelerometerData, Adafruit_BNO055::VECTOR_ACCELEROMETER);
  bno.getEvent(&gravityData, Adafruit_BNO055::VECTOR_GRAVITY);

  sensorData.roll = orientationData.orientation.y;
  sensorData.pitch = orientationData.orientation.z;
  sensorData.heading = orientationData.orientation.x;
}

void IMU_calibration() {

  uint8_t system, gyro, accel, mag = 0;
  bno.getCalibration(&system, &gyro, &accel, &mag);
  SERIAL_DEBUG_LN();
  SERIAL_DEBUG("Calibration: Sys=");
  SERIAL_DEBUG(system);
  SERIAL_DEBUG(" Gyro=");
  SERIAL_DEBUG(gyro);
  SERIAL_DEBUG(" Accel=");
  SERIAL_DEBUG(accel);
  SERIAL_DEBUG(" Mag=");
  SERIAL_DEBUG_LN(mag);
}

bool temperature_sensor_init() {

  sensor_DS18.begin();

  uint8_t resolution = sensor_DS18.getResolution();

  sensor_DS18.setResolution(SENSOR_BIT_RESOL);
  resolution = sensor_DS18.getResolution();
  SERIAL_DEBUG("Setting DS18B20 temperature sensor resolution to 0.50 C: ");
  SERIAL_DEBUG(resolution);
  SERIAL_DEBUG_LN("bits");

  // Searching sensors
  SERIAL_DEBUG_LN("Searching temp sensors...");
  SERIAL_DEBUG("Found: ");
  byte numSensorsFound = sensor_DS18.getDeviceCount();
  SERIAL_DEBUG(numSensorsFound);
  SERIAL_DEBUG_LN(" sensors");
  if (numSensorsFound < DS18_NR) {
    SERIAL_DEBUG(" Missing ");
    int miss_ds18 = DS18_NR - numSensorsFound;
    SERIAL_DEBUG(miss_ds18);
    SERIAL_DEBUG_LN(" DS18B20 temperature sensors");
  } else {
    SERIAL_DEBUG_LN("All DS18B20 temperature sensors found");
  }
  // If found any, show address
  if (numSensorsFound >= 1) {
    for (byte sens_i = 0; sens_i < numSensorsFound; sens_i++) {
      DeviceAddress sens_temp_addr;  // 8 byte array (uint8_t)
      // get adddres of the sensor
      sensor_DS18.getAddress(sens_temp_addr, sens_i);
      // compare the address with the sensors
      if (comp_dev_addr(sens_temp_addr, TEMP_CUBESAT_ADDR)) {
        temp_cubesat_found = true;
        SERIAL_DEBUG("General cubesat sensor address found: ");  // inside cubesat, outside battery box
      } else if (comp_dev_addr(sens_temp_addr, TEMP_BAT_BOX_ADDR)) {
        temp_bat_box_found = true;
        SERIAL_DEBUG("Battery box sensor address found:     ");
      } else if (comp_dev_addr(sens_temp_addr, TEMP_BAT_LEFT_ADDR)) {
        SERIAL_DEBUG("Left heatmat sensor address found:    ");
        temp_bat_left_found = true;
      } else if (comp_dev_addr(sens_temp_addr, TEMP_BAT_RIGHT_ADDR)) {
        SERIAL_DEBUG("Right heatmat sensor address found:   ");
        temp_bat_right_found = true;
      } else if (comp_dev_addr(sens_temp_addr, TEMP_BAT_DOWN_ADDR)) {
        SERIAL_DEBUG("Down heatmat sensor address found:    ");
        temp_bat_down_found = true;
      } else {
        SERIAL_DEBUG("Unkown temperature sensor address found:    ");
      }
      // print the address
      prnt_dev_addr(sens_temp_addr);  // print the address
    }

    // after the loop, check if there is a missing temperature sensor:
    if (!temp_cubesat_found) {
      SERIAL_DEBUG("WARNING: General cubesat DS18B20 temperature sensor address not found, address:  ");
      prnt_dev_addr(TEMP_CUBESAT_ADDR);
    }
    if (!temp_bat_box_found) {
      SERIAL_DEBUG("WARNING: Battery box DS18B20 temperature sensor address not found, address:  ");
      prnt_dev_addr(TEMP_BAT_BOX_ADDR);
    }
    if (!temp_bat_right_found) {
      SERIAL_DEBUG("WARNING: Rigth heatmat DS18B20 temperature sensor address not found, address:  ");
      prnt_dev_addr(TEMP_BAT_RIGHT_ADDR);
    }
    if (!temp_bat_left_found) {
      SERIAL_DEBUG("WARNING: Left heatmat DS18B20 temperature sensor address not found, address:  ");
      prnt_dev_addr(TEMP_BAT_LEFT_ADDR);
    }
    if (!temp_bat_down_found) {
      SERIAL_DEBUG("WARNING: Down heatmat DS18B20 temperature sensor address not found, address:  ");
      prnt_dev_addr(TEMP_BAT_DOWN_ADDR);
    }

    return true;
  } else {
    SERIAL_DEBUG_LN("No DS18B20 temperature sensors found");
    return false;
  }
}

File openDataFile(const char *filename) {
  File dataFile = SD.open(filename, FILE_WRITE);
  if (!dataFile) {
    SERIAL_DEBUG("ERROR: Failed to open data file: ");
    SERIAL_DEBUG_LN(filename);
  }
  return dataFile;
}
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

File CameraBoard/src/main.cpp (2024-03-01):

#include <iostream>
#include <fstream>
#include <filesystem>
#include <vector>

//Definimos el formato del pixel
struct Pixel {
    uint8_t r, g, b;
    Pixel() = default;
    Pixel(uint8_t r, uint8_t g, uint8_t b) : r(r), g(g), b(b) {}
};

//Creamos la funcion para convertir la imagen de NV12 a RGB
auto NV12toRGB2(const std::vector<uint8_t> &nv12, int width, int height){
    //La primera parte del archivo define la luminancia (Y)
    int yLimit = width*height;
    auto y = std::vector<uint8_t>();
    y.assign(nv12.begin(), nv12.begin() + yLimit);
    //La segunda parte define la crominancia (Cb y Cr)
    auto cbcr = std::vector<uint8_t>();
    cbcr.assign(nv12.begin() + yLimit, nv12.end());

    auto cb = std::vector<uint8_t>(width*height);
    auto cr = std::vector<uint8_t>(width*height);

    //Definimos la conversion de luminancia y crominancia a RGB
    auto fromNV12 = [](double Y, double Cb, double Cr) {
        return Pixel{
            static_cast<uint8_t>(std::min(255.0, std::max(0.0, Y + 1.370705 * Cr))),
            static_cast<uint8_t>(std::min(255.0, std::max(0.0, Y - 0.337633 * Cb - 0.698001 * Cr))),
            static_cast<uint8_t>(std::min(255.0, std::max(0.0, Y + 1.732446 * Cb)))
        };
    };
    int index = 0;
    auto planar = std::vector<Pixel>(width*height);

    //Recorremos el archivo NV12 aplicando la conversion
    for (int row = 0; row < height; row+=2){
        for (int col = 0; col < width; col+=2){
            double Y1 = y[row * width + col] - 16;
            double Y2 = y[row * width + col + 1] - 16;
            double Y3 = y[(row + 1) * width + col] - 16;
            double Y4 = y[(row + 1) * width + col + 1] - 16;
            double Cb = cbcr[index] - 128 , Cr = cbcr[index + 1] - 128 ;
            planar[row * width + col] = fromNV12(Y1, Cb, Cr);
            planar[row * width + col + 1] = fromNV12(Y2, Cb, Cr);
            planar[(row + 1) * width + col] = fromNV12(Y3, Cb, Cr);
            planar[(row + 1) * width + col + 1] = fromNV12(Y4, Cb, Cr);

            index += 2;
        }
    }
    return planar;
}

std::vector<double> CalculateNDVI(std::vector<Pixel> red, std::vector<Pixel> nir)
{
    auto auxNDVI = std::vector<double>{};
    auxNDVI.reserve(red.size());
    for (int i = 0; i < static_cast<int>(red.size()); ++i) {
        //auto nirValue = (static_cast<double>(nir[i].r + nir[i].g + nir[i].b)/3);
        auto nirValue = static_cast<double>(nir[i].r);
        //nirValue = std::min(std::max(0.0, nirValue), 255.0);
        auto value = (nirValue - red[i].r)/(nirValue + red[i].r);
        auxNDVI.push_back(value);
    }
    return auxNDVI;
}

int main(int argc, char* argv[]) {
    //Definimos las dimensiones de la imagen
    const int width = 4056;
    const int height = 3040;
    //const int RED_INDEX = 0;
    //const int NIR_INDEX = 1;

    //Comprobamos que el numero de argumentos de entrada sea el correcto
    if (argc < 3 || argc > 4) {
        std::cerr << "Usage: " << argv[0] << " input_path output_path" << std::endl;
        return 1;
    }

    //El primer argumento debe ser el directorio de donde se extraen las imagenes
    //No tiene por que ser el directorio final, puede ser una carpeta con mas carpetas en su interior
    //El segundo argumento es el directorio en donde se guardan las imagenes
    //El programa creara la carpeta final si esta no existe, las anteriores deben existir
    std::filesystem::path input_path(argv[1]);
    std::filesystem::path output_path(argv[2]);

    if (!std::filesystem::exists(input_path)) {
        std::cerr << "Input image does not exist." << std::endl;
        return 2;
    }

    if (!std::filesystem::exists(output_path.parent_path())) {
        std::filesystem::create_directory(output_path.parent_path());
    }

    std::ifstream input_stream(input_path, std::ios::binary);
    input_stream.seekg(0, std::ios::end);
    auto input_size = input_stream.tellg();
    input_stream.seekg(0, std::ios::beg);

    auto input_data = std::vector<uint8_t>(input_size);

    input_stream.read((char *) input_data.data(), input_size);
    auto rgbPlanar = NV12toRGB2(input_data, width, height);
    /*
    if (argc == 4) {
        std::filesystem::path calibrationPath(argv[3]);
        if (!std::filesystem::exists(calibrationPath)) {
            std::cerr << "Calibration directory does not exist." << std::endl;
            return 3;
        }

        auto whiteCalPath = calibrationPath / "white.ppm";
        auto blackCalPath = calibrationPath / "black.ppm";

        if (!std::filesystem::exists(whiteCalPath) || !std::filesystem::exists(blackCalPath)) {
            std::cerr << "Calibration directory is empty." << std::endl;
            return 4;
        }
        
        auto readPPM = [] (std::filesystem::path &inputPath) {
            auto imageStream = std::ifstream(inputPath, std::ios::binary);
            imageStream.seekg(0, std::ios::end);
            auto fileSize = imageStream.tellg();
            imageStream.seekg(0, std::ios::beg);

            // Removing header
            std::string fileType;
            std::string widthStr;
            std::string heightStr;
            std::string maxValue;

            long int headerBytes = 0;
            int headerParts = 0;
            bool comment = false;
            for (;;) {
                char currentValue;
                imageStream >> currentValue;
                if (!comment) {
                    if (currentValue == '#') { comment = true; }
                    else if (currentValue == ' ') { headerParts++; }
                    else {
                        if (headerParts == 0) fileType += currentValue;
                        else if (headerParts == 1) widthStr += currentValue;
                        else if (headerParts == 2) heightStr += currentValue;
                        else if (headerParts == 3) maxValue += currentValue;
                    }
                    if (headerParts == 3 && currentValue == '\n') break; 
                } else { if (currentValue == '\n') { comment = false; } }
                headerBytes++;
            }
	    const auto dataSize = fileSize - headerBytes;
            auto imageData = std::vector<uint8_t>(dataSize);
            auto imageWidth = std::stoi(widthStr);
            auto imageHeight = std::stoi(heightStr);
            imageStream.read((char *) imageData.data(), imageData.size());
            auto image = std::vector<Pixel>{};
            image.reserve(imageWidth*imageHeight);
            for (int i = 0; i < imageHeight*imageWidth*3; i+=3) {
                image.emplace_back(
                    imageData[i], imageData[i + 1], imageData[i + 2]
                );
            }
            return image;
        };

        auto whiteCal = readPPM(whiteCalPath);
        auto blackCal = readPPM(blackCalPath);
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

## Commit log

2023-05-09 First commit for the Bentayga repo
    [Lora_new_sender.ino, lora_receiver.ino, lora_sender.ino]
2023-05-16 WORKING: Ground station receiving parameters from Arduino via serial, NOT GPS
2023-05-16 Some modification for arduino
2023-06-05 Get DS18B20 temp sensor address from Arduino
2023-06-05 Get temperature fron ID of temp sensors
    Using OneWire Ds18B20 sensors
2023-06-05 Include temperature sensor resolution
2023-06-05 Add OneWire + Dallas Temperature libraries
2023-06-05 rename folder to temperature
    from temp_sensor
2023-06-06 Temperature control with heatpad + temp sensors
2023-06-08 App and FW update
    [mkr1310v3-bottom.stl]
2023-06-08 Add info about battery voltage
    In case you use a >12V battery (14.4V in our case)
2023-07-13 Add Jetson Nano code
2023-07-28 DS18B20 temp sensor identification in Arduino code
    Addresses have been included in the code, and check if they are found
    also include some documentation
    modified: Firmware/FW_FligthManager/Flight_manager_2.0/Flight_manager_2.0.ino
    Firmware/readme.md README.md
    new file: imgs/cubesat_izq_dcha.jpeg imgs/cubesat_izq_dcha_sm.jpeg
2023-07-28 Include missing DS18B20 temp sensors in code
    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
    [Flight_manager_2.0.ino]
2023-07-28 Add DS18 temp sensors report in Arduino code
    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
2023-07-29 Include CRC Arduino + update temp ground station
    Firmware/ground_station/ground_station.ino
    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
2023-07-30 Add CAD for supporting switches
    new file: cad/switch_support.stl
    cad/cubesat_switches.png
    cad/switch_support.step
    [switch_support.step, switch_support.stl]
2023-07-31 Correct CRC generated in OBC, not in receptor
    Still need verification and make sure the receptor calculates it
    [Flight_manager_2.0.ino]
2023-08-01 Create README for camera capturing platform
2023-08-02 Add CAD + svg for lasercut
    [camera_support_toprint.FCStd, camera_support_toprint.step, camera_support_toprint.stl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]
2023-08-03 Add IGES and DXF files to cut the plates
    [placa_cielo.dxf, placa_cielo.iges, placa_down_dipole.dxf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]
2023-08-03 Include temperature control with heatmat
2023-08-04 Change heatmat pin to 1, conflict 0 with IMU
    It seems that the IMU uses pin 0 and could not set the signal for the
    MOSFET
    modified: Firmware/FW_FlightManager/Flight_manager_2.0/Flight_manager_2.0.ino
2023-08-04 Fix bug with PWM levels
    Heat level 3 was doing integer multiplication by (3/4), which resulted
    in zero
    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
    [Flight_manager_2.0.ino]
2023-08-06 Add Flight manager schematic + BOM
    BOM need revision, as well as the Arduino schematic
    [bom_bentayga_cubesat.ods]
2023-08-11 Move slot of M5 camera support
    [bom_bentayga_cubesat.ods, camera_support_toprint.FCStd, camera_support_toprint.step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]
2023-08-12 Organize readme + doc connections to Jetson Nano
2023-08-13 Start assembly documentation
2023-08-13 Ongoing assembly documentation
2023-08-13 Continue with assembly instructions
2023-08-13 Assembly documentation almost finished
2023-08-17 Added better visual for serial terminal in arduino for ground station
2023-08-23 Update app for ground station. Batt_temp graph
2023-09-12 Fixed app.py (before 3d_app.py)
    [2023-09-05_22-04-09.csv, 2023-09-05_22-21-11.csv, 2023-09-05_23-20-15.csv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]
2023-09-12 Fixed app.py and graphic tools
    [2023-09-05_22-04-09.csv, 2023-09-05_22-21-11.csv, 2023-09-05_23-20-15.csv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]
2023-09-12 Revert "Fixed app.py (before 3d_app.py)"
    This reverts commit e0838c1ce3bd61790ca1e011898c0a8285c860b8.
    [2023-09-12_10-00-29.csv, 2023-09-12_10-09-23.csv, mkr1310v3-bottom.stl]
2023-09-12 APP WORKING:Update everything to the last app version
    [2023-09-05_22-04-09.csv, 2023-09-05_22-21-11.csv, 2023-09-05_23-20-15.csv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]
2023-09-13 Add CAD of smaller version of switch support
    To make room for the larger antenna
    new file: cad/fcad/switch_support_cut.FCStd
    cad/step/switch_support_cut.step
    cad/stl/switch_support_cut.stl
    [switch_support_cut.FCStd, switch_support_cut.step, switch_support_cut.stl]
2023-09-16 Add optional arduino SRAM free memory informationd
    using a define
    Need to install https://github.com/mpflaga/Arduino-MemoryFree
    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
2023-09-16 Changed pin7 of Arduino from Jetson Nano
    Also changes in how the camera info from Jetson Nano is stored
    imgs/cubesat_schematic.jpg imgs/cubesat_schematic_sm.jpg
    imgs/jetson_schematic.jpg imgs/jetson_schematic_sm.jpg
    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
2023-09-16 Debug directive to avoid using serial print
    When not debugging, it will not use the UART to print information
    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
    [Flight_manager_2.0.ino]
2023-09-16 Arduino sketch to scan i2c addresses
    new file: Firmware/i2c_address.txt Firmware/i2c_scan/i2c_scan.ino
